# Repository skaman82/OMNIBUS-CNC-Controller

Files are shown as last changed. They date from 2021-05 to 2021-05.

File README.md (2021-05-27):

# OMNIBUS-CNC-Controller (WORK IN PROGRESS)
CNC Control Project (GRBL and ESTLCAM based). Please dont' sell the boards published here without my consent.

## OMNIBUS ESTLCAM Controller</br>
### FINISHED
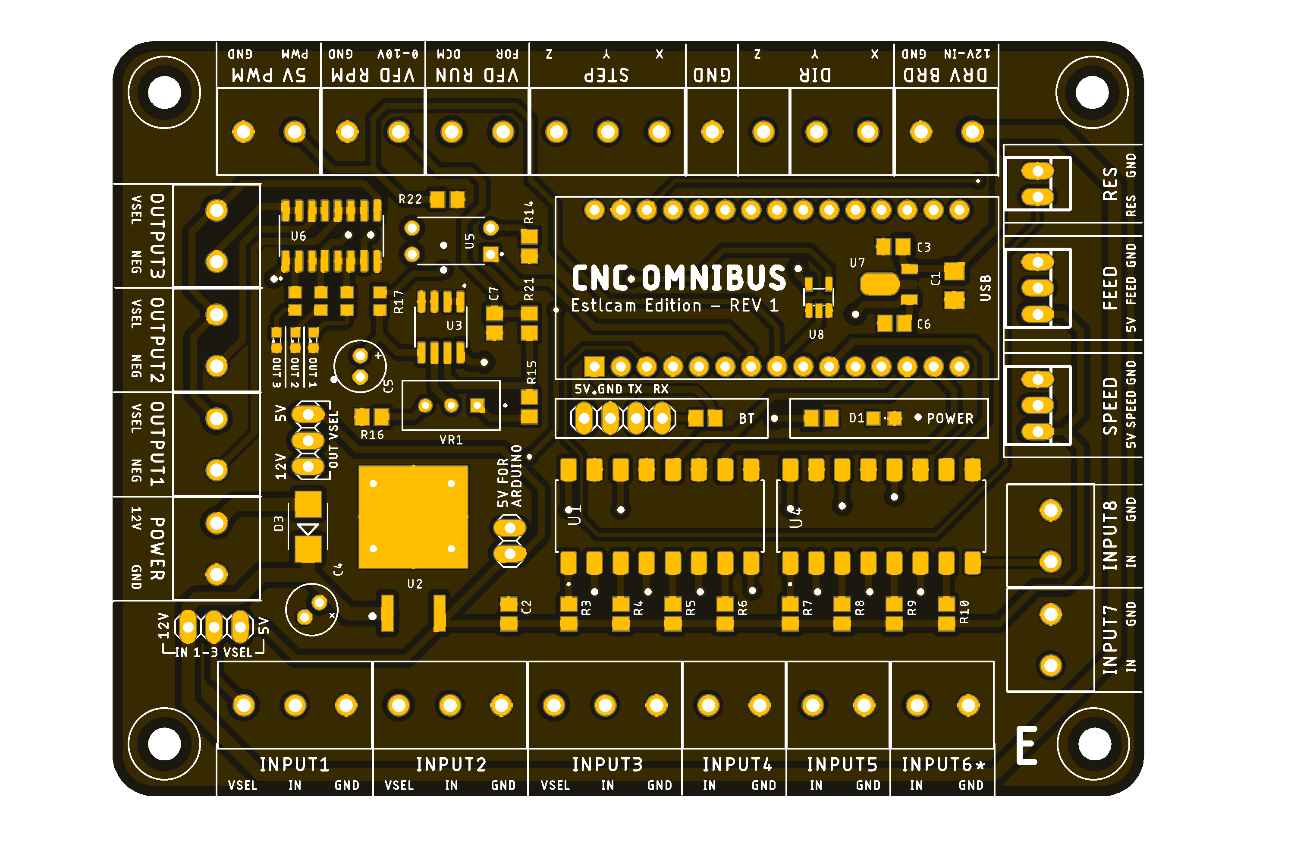
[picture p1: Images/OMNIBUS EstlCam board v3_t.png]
</br>
• 8 inputs for sensors and buttons (IN6 is usable if you remoove the LED "L" from the Nano)</br>
• All inputs are isolated with optocouplers</br>
• Inputs 1-3 have selectable voltage (5/12v) so you can connect inductive proximity sensors directly</br>
• VFD outputs (Spindle ON/OFF and RPM control)</br>
• 5V PWM output</br>
• 3 Outputs for relays - the outputs have selectable voltage (5/12v) - OUT3 is automatically enabled on spindle ON</br>
• Feed/Speed override connectors (JST XH 3P)</br>
• Header for bluetooth serial module (HC-05)</br>
• Screw-Terminals for easy connection</br>
• Connector for the DRV-Shield</br>
</br>
## OMNIBUS GRBL 1.1 Controller - also ESTLCAM compatible</br>
### FINISHED
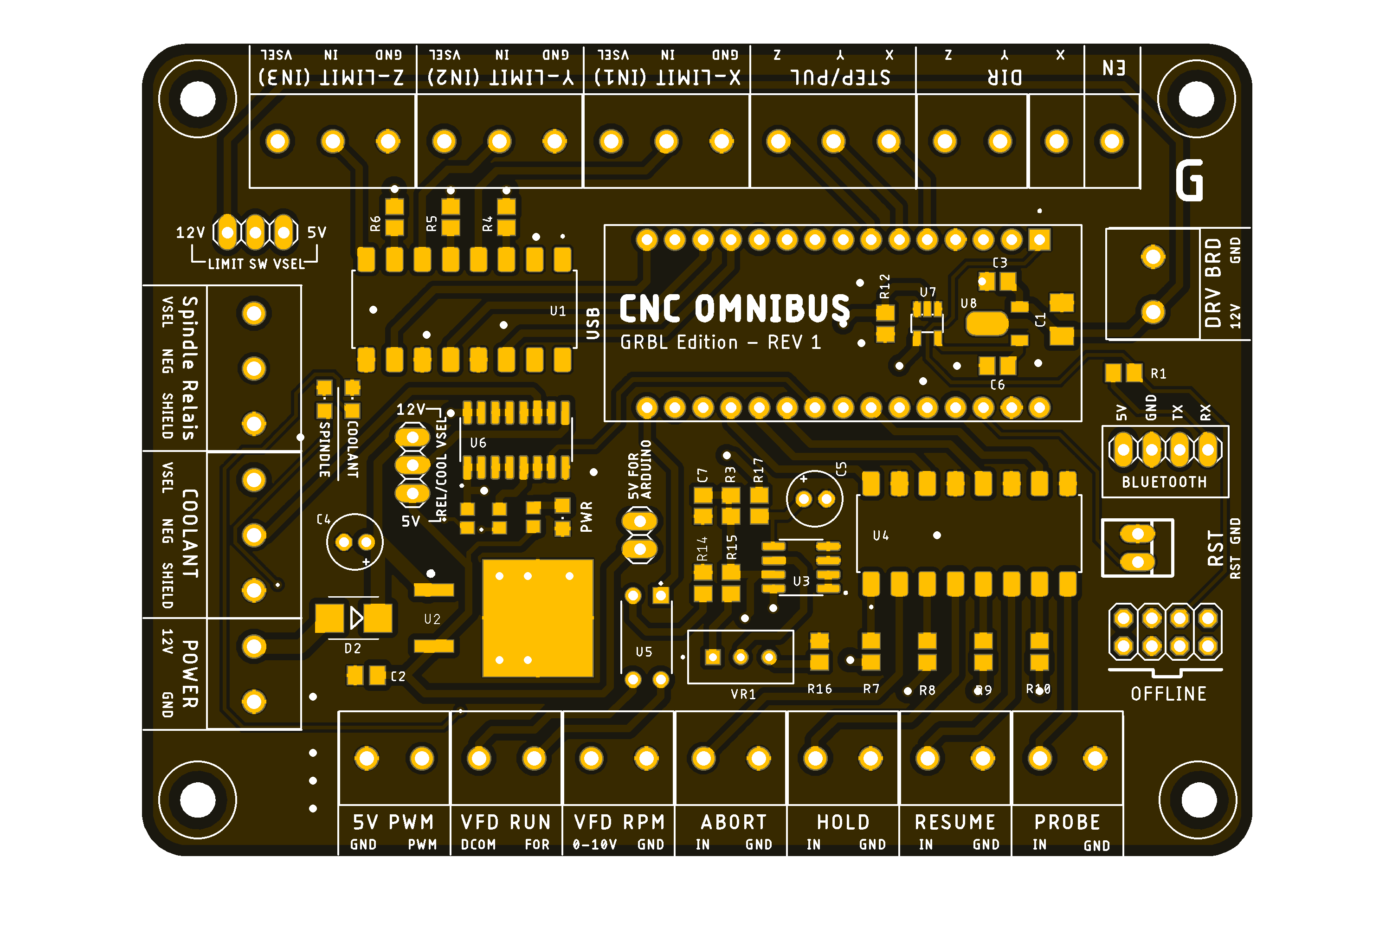
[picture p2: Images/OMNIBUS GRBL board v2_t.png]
</br>
• Limit-Inputs XYZ have selectable voltage (5/12v) so you can connect inductive proximity sensors directly</br>
• ABORT/HOLD/RESUME/PROBE inputs</br>
• All inputs are isolated with optocouplers</br>
• VFD outputs (Spindle ON/OFF and RPM control)</br>
• 5V PWM Output</br>
• 2 Outputs for relay (SPINDLE_RELAIS / COOLANT) - the outputs have selectable voltage (5/12v) - SPINDLE RELAY is automatically enabled on spindle ON</br>
• Header for bluetooth serial module (HC-05)</br>
• Header for offline controller</br>
• Screw-Terminals for easy connection</br>
• Connector for the DRV-Shield</br>

NOTE: To use the "SPINDLE RELAY" and "VFD RUN" Outputs, please uncomment "define USE_SPINDLE_DIR_AS_ENABLE_PIN" in the GRBL config.h file.
</br>
## OMNIBUS DRV SHIELD (mounts on top the controll PCB with spacers)</br>
### Experimental stage
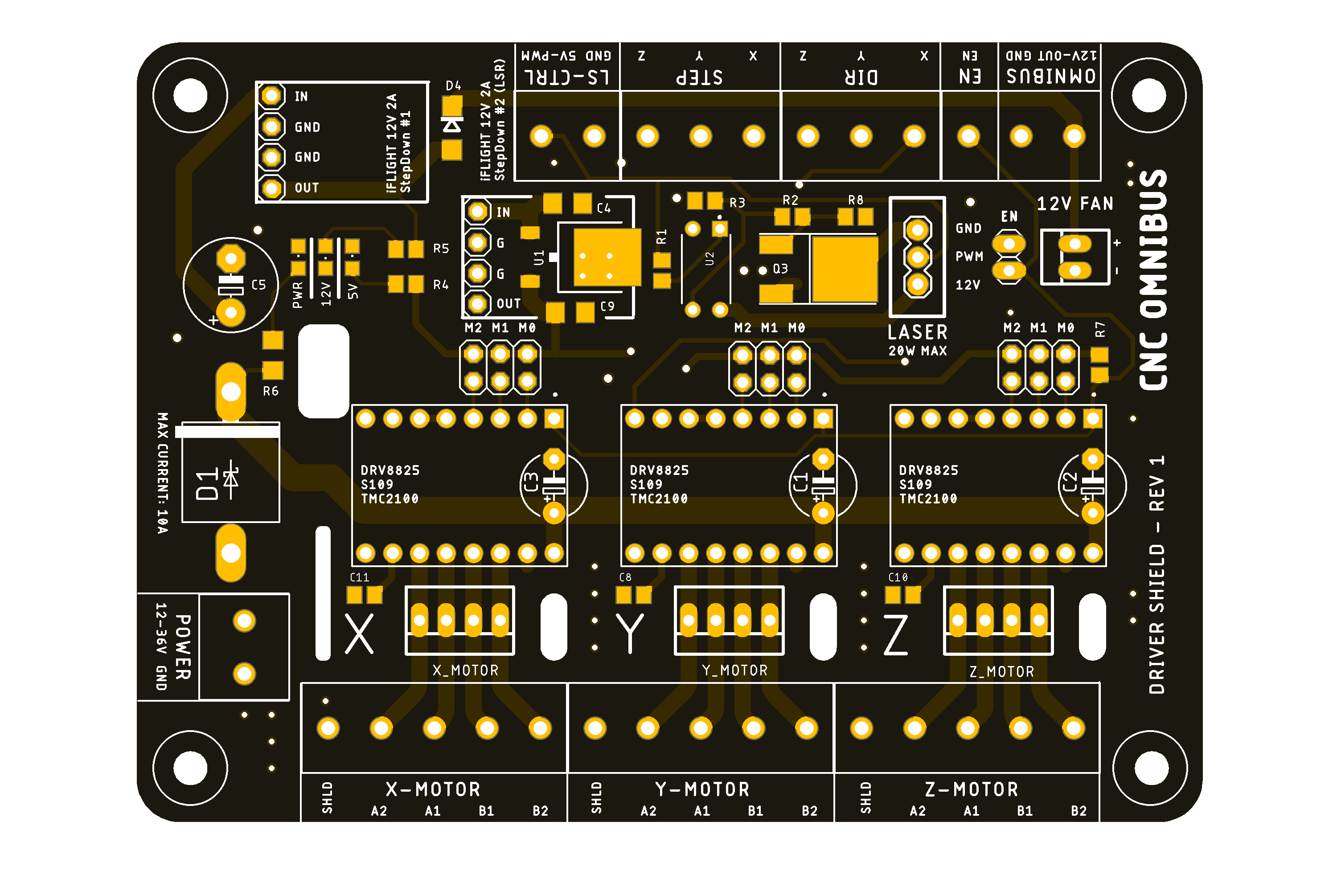
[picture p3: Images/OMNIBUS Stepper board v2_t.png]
</br>
• Up to 10A current support (2oz copper PCB required)</br>
• 3-Axis stepper driver support (DRV8825/S109/TMC2100) with stepping config jumpers</br>
• Header for laser module (3p)</br>
• Laser module safety switch - PWM controlled</br>
• Header for an extra 12V 2A BEC to power a laser module (20w max)</br>
• 12V fan header</br>
• 12V Power supply for the OMNIBUS controller (so you don't need an extra 12v PSU for the controll board)</br>
• Screw-Terminals for easy connection</br>

NOTE: If powerting the OMNIBUS Controller with the DRV Shield, use a heatsink on the 12V LDO and provide good airflow - the LDO is getting hot and will
shut down if thermal protection kicks in.

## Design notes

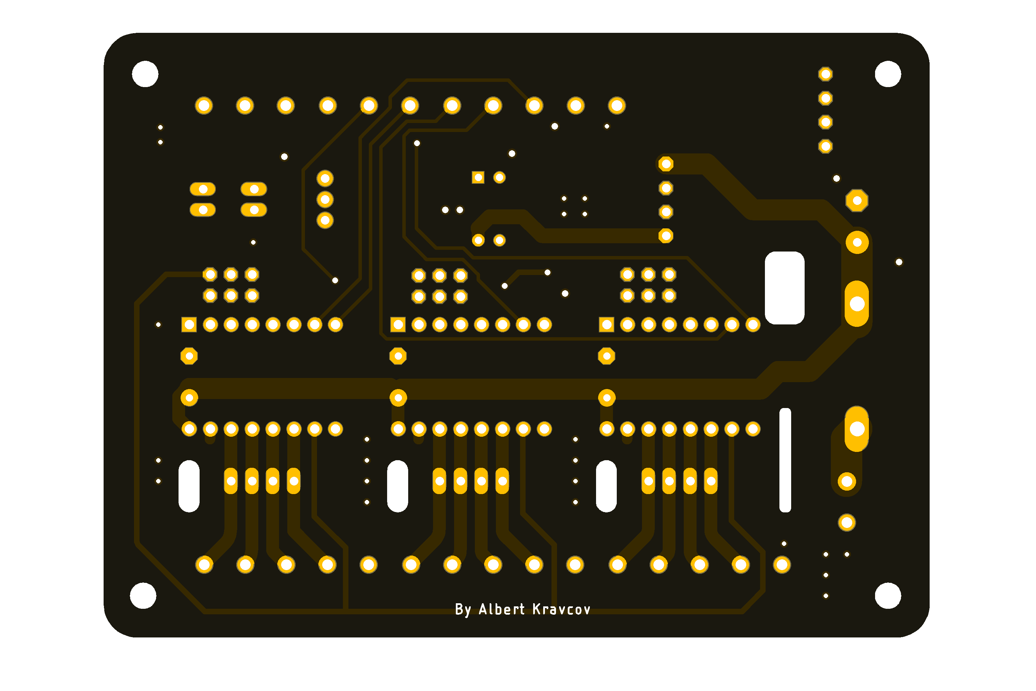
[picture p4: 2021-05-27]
Images/OMNIBUS Stepper board v2_b.png

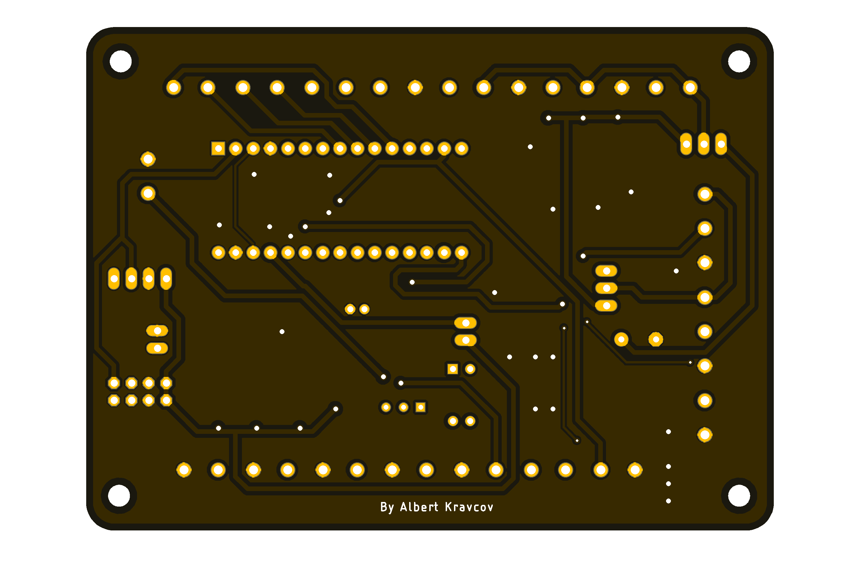
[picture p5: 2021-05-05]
Images/OMNIBUS GRBL board v2_b.png

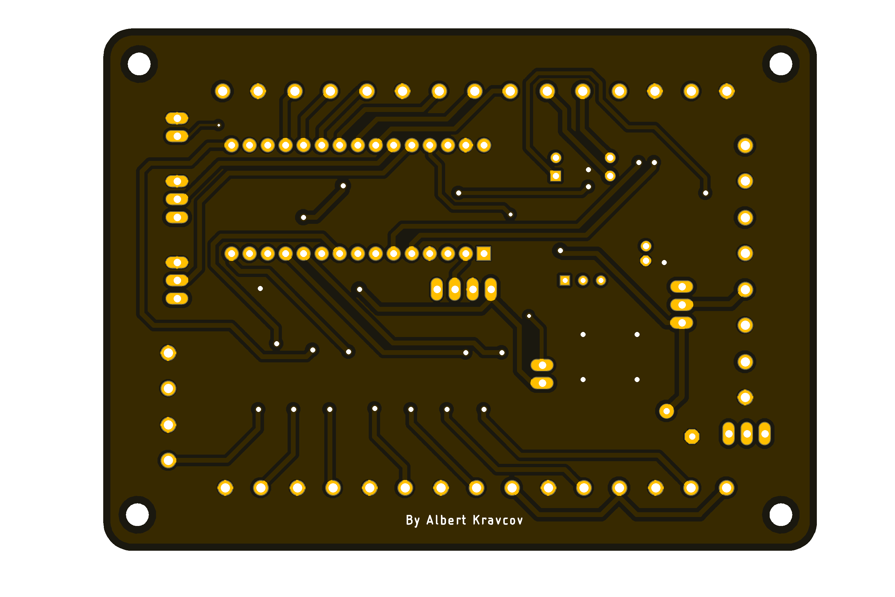
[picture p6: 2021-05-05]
Images/OMNIBUS EstlCam board v3_b.png

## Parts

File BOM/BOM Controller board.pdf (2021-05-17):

### EstlCam board v3

Part | Value | Device | Package | Description | price
BT | 2.54 pin header | PINHD-1X4 | 1X04 | PIN HEADER | 0
C1 | 0.33uF 50v | C-EUC1206 | C1206 Tantal | CAPACITOR, European symbol | 1,18
C2 | 100nf | C-EUC0805 | C0805 | CAPACITOR, European symbol | 0,054
C3 | 100nf | C-EUC0805 | C0805 | CAPACITOR, European symbol | 0,054
C4 | 220uf 25v | CPOL-EUE5-6 | E5-6 | POLARIZED CAPACITOR, European symbol | 0,52
C5 | 22uf | CPOL-EUE2-5 | E2-5 | POLARIZED CAPACITOR, European symbol | 0,52
C6 | 100nf | C-EUC0805 | C0805 | CAPACITOR, European symbol | 0,054
C7 | 100nf | C-EUC0805 | C0805 | CAPACITOR, European symbol | 0,054
D1 | green | LED1206 | LED-1206 | LED (Generic) | 0,23
D3 | SS36 | ES2D | SMB | DIODE | 0,34
IN1 | KF301-2P | 691131710002 | 691131710002 | WR-TBL Terminal block - CUU5/2 CUU5/2GR - 2 Pins;=>Code : Con_TBL_Screw_PClamp_5.00_6911317100xx_691131710002 | 0,125
IN2 | KF301-2P | 691131710002 | 691131710002 | WR-TBL Terminal block - CUU5/2 CUU5/2GR - 2 Pins;=>Code : Con_TBL_Screw_PClamp_5.00_6911317100xx_691131710002 | 0,125
IN3 | KF301-2P | 691131710002 | 691131710002 | WR-TBL Terminal block - CUU5/2 CUU5/2GR - 2 Pins;=>Code : Con_TBL_Screw_PClamp_5.00_6911317100xx_691131710002 | 0,125
IN4 | KF301-2P | 691131710002 | 691131710002 | WR-TBL Terminal block - CUU5/2 CUU5/2GR - 2 Pins;=>Code : Con_TBL_Screw_PClamp_5.00_6911317100xx_691131710002 | 0,125
IN5 | KF301-2P | 691131710002 | 691131710002 | WR-TBL Terminal block - CUU5/2 CUU5/2GR - 2 Pins;=>Code : Con_TBL_Screw_PClamp_5.00_6911317100xx_691131710002 | 0,125
IN6 | KF301-2P | 691131710002 | 691131710002 | WR-TBL Terminal block - CUU5/2 CUU5/2GR - 2 Pins;=>Code : Con_TBL_Screw_PClamp_5.00_6911317100xx_691131710002 | 0,125
IN_V_SEL | 2.54 pin header | PINHD-1X3 | 1X03 | PIN HEADER | 0
JP1 | 2.54 pin header | PINHD-1X2 | 1X02 | PIN HEADER | 0
IN7 | KF301-2P | 691131710002 | 691131710002 | WR-TBL Terminal block - CUU5/2 CUU5/2GR - 2 Pins;=>Code : Con_TBL_Screw_PClamp_5.00_6911317100xx_691131710002 | 0,125
IN8 | KF301-3P | 691131710003 | 691131710003 | WR-TBL Terminal block - CUU5/3 - 3 Pins;=>Code : | 0,125
DIR1 | KF301-3P | 691131710003 | 691131710003 | WR-TBL Terminal block - CUU5/3 - 3 Pins;=>Code : | 0,125
DIR2 | KF301-3P | 691131710003 | 691131710003 | WR-TBL Terminal block - CUU5/3 - 3 Pins;=>Code : | 0,125
LED2 | red | LED_ESML0603 | LED_SML0603 | LED | 0,23
LED3 | red | LED_ESML0603 | LED_SML0603 | LED | 0,23
LED4 | red | LED_ESML0603 | LED_SML0603 | LED | 0,23
OUT3 | KF301-2P | 691131710002 | 691131710002 | WR-TBL Terminal block - CUU5/2 CUU5/2GR - 2 Pins;=>Code : Con_TBL_Screw_PClamp_5.00_6911317100xx_691131710002 | 0,125
VFD | KF301-2P | 691131710002 | 691131710002 | WR-TBL Terminal block - CUU5/2 CUU5/2GR - 2 Pins;=>Code : Con_TBL_Screw_PClamp_5.00_6911317100xx_691131710002 | 0,125
RPM | KF301-2P | 691131710002 | 691131710002 | WR-TBL Terminal block - CUU5/2 CUU5/2GR - 2 Pins;=>Code : Con_TBL_Screw_PClamp_5.00_6911317100xx_691131710002 | 0,125
PWM | KF301-2P | 691131710002 | 691131710002 | WR-TBL Terminal block - CUU5/2 CUU5/2GR - 2 Pins;=>Code : Con_TBL_Screw_PClamp_5.00_6911317100xx_691131710002 | 0,125
OUT1 | KF301-2P | 691131710002 | 691131710002 | WR-TBL Terminal block - CUU5/2 CUU5/2GR - 2 Pins;=>Code : Con_TBL_Screw_PClamp_5.00_6911317100xx_691131710002 | 0,125
POW | KF301-2P | 691131710002 | 691131710002 | WR-TBL Terminal block - CUU5/2 CUU5/2GR - 2 Pins;=>Code : Con_TBL_Screw_PClamp_5.00_6911317100xx_691131710002 | 0,125
OUT_V_SEL | 2.54 pin header | PINHD-1X3 | 1X03 | PIN HEADER | 0
PWM | KF301-2P | 691131710002 | 691131710002 | WR-TBL Terminal block - CUU5/2 CUU5/2GR - 2 Pins;=>Code : Con_TBL_Screw_PClamp_5.00_6911317100xx_691131710002 | 0,125
OUT2 | KF301-2P | 691131710002 | 691131710002 | WR-TBL Terminal block - CUU5/2 CUU5/2GR - 2 Pins;=>Code : Con_TBL_Screw_PClamp_5.00_6911317100xx_691131710002 | 0,125
R1 | 1k | R-EU_R0805 | R0805 | RESISTOR, European symbol | 0,036
R2 | 220 | R-EU_R0805 | R0805 | RESISTOR, European symbol | 0,036
R3 | 220 | R-EU_R0805 | R0805 | RESISTOR, European symbol | 0,036
R4 | 220 | R-EU_R0805 | R0805 | RESISTOR, European symbol | 0,036
R5 | 220 | R-EU_R0805 | R0805 | RESISTOR, European symbol | 0,036
R6 | 220 | R-EU_R0805 | R0805 | RESISTOR, European symbol | 0,036
R7 | 220 | R-EU_R0805 | R0805 | RESISTOR, European symbol | 0,036
R8 | 220 | R-EU_R0805 | R0805 | RESISTOR, European symbol | 0,036
R9 | 220 | R-EU_R0805 | R0805 | RESISTOR, European symbol | 0,036
R10 | 220 | R-EU_R0805 | R0805 | RESISTOR, European symbol | 0,036
R11 | 220 | R-EU_R0603 | R0603 | RESISTOR, European symbol | 0,036
R12 | 220 | R-EU_R0603 | R0603 | RESISTOR, European symbol | 0,036
R13 | 220 | R-EU_R0603 | R0603 | RESISTOR, European symbol | 0,036
R14 | 220 | R-EU_R0805 | R0805 | RESISTOR, European symbol | 0,036
R15 | 1k | R-EU_R0805 | R0805 | RESISTOR, European symbol | 0,036
R16 | 1k | R-EU_R0805 | R0805 | RESISTOR, European symbol | 0,036
R17 | 4k7 | R-EU_R0603 | R0603 | RESISTOR, European symbol | 0,036
R21 | 1k | R-EU_R0805 | R0805 | RESISTOR, European symbol | 0,036
R22 | 4k7 | R-EU_R0805 | R0805 | RESISTOR, European symbol | 0,036
FEED | jst xh 3p | 22-23-2031 | 22-23-2031 | .100 (2.54mm) Center Header - 3 Pin" | 0,255
RESET | jst xh 2p | 22-23-2021 | 22-23-2021 | .100 (2.54mm) Center Header - 2 Pin" | 0,255
SPEED | jst xh 3p | 22-23-2031 | 22-23-2031 | .100 (2.54mm) Center Header - 3 Pin" | 0,255
STEP | KF301-3P | 691131710003 | 691131710003 | WR-TBL Terminal block - CUU5/3 - 3 Pins;=>Code : | 0,125
TB1 | Pin-Header FEM | ARDUINO_NANO | SHIELD_ARDUINO_NANO | Arduino Nano, Through Hole | 1,0
U1 | LTV-847S | LTV-847S | SOIC254P1016X460-16N | Optocoupler DC-IN 4-CH Transistor DC-OUT 16-Pin PDIP SMD Check prices | 1,08
U2 | MC7805C | MC7805C | TO254P1515X470-3N | 5V Positive voltage regulator ICs Check prices | 2,29
U3 | LM358M/NOPB | LM358M/NOPB | SOIC127P599X175-8N | Check prices Check prices | 0,25
U4 | LTV-847S | LTV-847S | SOIC254P1016X460-16N | Optocoupler DC-IN 4-CH Transistor DC-OUT 16-Pin PDIP SMD Check prices | 1,08
U5 | PC817X3NSZ1B | PC817X3NSZ1B | DIP762W50P254L495H455Q4 | Optoisolator Transistor Output 1 Channel 4-DIP Check prices | 0,299
U6 | ULN2003AD | ULN2003AD | SOIC127P600X175-16N | Check prices | 0,27
U7 | L78L05ACU | L78L05ACU | SOT89 | 5V Positive voltage regulator SMD SOT89 Package 100mA | 0,6
U8 | 74AHC1G125 | SN74AHC1G125DCKR SOT23-5L | | | 0,375
VR1 | 10k | W103 | TRIM_POT | Res Cermet Trimmer10K Ohm 10% 0.5W 25(Elec)Turn 2.19mm (9.53 X 4.83 X 11.55mm) Pin Thru-Hole Tube Check prices | 1,9
JP | 3x | | 2.54 Headers and Jumpers | | 0,204
HT | Heatsink | 10x10x10mm | Heatsink | | 0,41
PCB | pcb fab | pcb+stencil cost | | | 3
POS | Montage und Tests | | | | 10
| | | | | BOM € | 30,278

1

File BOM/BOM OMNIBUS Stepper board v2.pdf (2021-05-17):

### OMNIBUS Stepper board v2

Part | Value | Device | Package | Description | Price
5V | green | LEDCHIPLED_0805 | CHIPLED_0805 | LED | 0,23
12V | green | LEDCHIPLED_0805 | CHIPLED_0805 | LED | 0,23
C1 | 100uf 50V | CPOL-EUE5-6 | E5-6 | POLARIZED CAPACITOR, European symbol | 1
C2 | 100uf 50V | CPOL-EUE5-6 | E5-6 | POLARIZED CAPACITOR, European symbol | 1
C3 | 100uf 50V | CPOL-EUE5-6 | E5-6 | POLARIZED CAPACITOR, European symbol | 1
C4 | 0.33uf | C-EUC1206 Tantal | C1206 | CAPACITOR, European symbol | 1,18
C5 | 100uf 50v | CPOL-EUE5-8.5 | E5-8,5 | POLARIZED CAPACITOR, European symbol | 0,5
C6 | 0.33uf 50v | C-EUC1206 Tantal | C1206 | CAPACITOR, European symbol | 1,18
C7 | 100nf | C-EUC0805 | C0805 | CAPACITOR, European symbol | 0,054
C8 | 100nf | C-EUC0805 | C0805 | CAPACITOR, European symbol | 0,054
C9 | 100nf | C-EUC1206 | C1206 | CAPACITOR, European symbol | 0,054
C10 | 100nf | C-EUC0805 | C0805 | CAPACITOR, European symbol | 0,054
C11 | 100nf | C-EUC0805 | C0805 | CAPACITOR, European symbol | 0,054
D1 | 10SQ045 | 10SQ050 | DIOAD885W125L910D885 | | 1
D2 | SS310 | SS310 | DO-214AC | SCHOTTKY DIODES 40Vpeak, 28Vrms 5A (SBD) SMA(DO-214AC) | 0,1
D4 | SS310 | SS310 | DO-214AC | SCHOTTKY DIODES 40Vpeak, 28Vrms 5A (SBD) SMA(DO-214AC) | 0,1
DIR | KF301-3P | 691131710003 | 691131710003 | WR-TBL Terminal block - CUU5/3 - 3 Pins;=>Code : | 0,125
EN-LOW | pin header and jumper | PINHD-1X2 | 1X02 | PIN HEADER | 0
FAN | JST XH 2p | 22-23-2021 | 22-23-2021 | .100 (2.54mm) Center Header - 2 Pin" | 0,255
J1 | JST XH 3p | CONN_03 | 1X03 | Multi connection point. Often used as Generic Header-pin footprint for 0.1 inch spaced/style header connections | 0,255
JP1 | BEC wire | PINHD-1X1 | 1X01 | PIN HEADER | 0
JP2 | BEC wire | PINHD-1X1 | 1X01 | PIN HEADER | 0
JP3 | BEC wire | PINHD-1X1 | 1X01 | PIN HEADER | 0
JP4 | BEC wire | PINHD-1X1 | 1X01 | PIN HEADER | 0
JP_X | pin header double row | PINHD-2X3 | 2X03 | PIN HEADER | 0,2
JP_Y | pin header double row | PINHD-2X3 | 2X03 | PIN HEADER | 0,2
JP_Z | pin header double row | PINHD-2X3 | 2X03 | PIN HEADER | 0,2
K7 | KF301-5P (or 2+3p) | 691131710005 | 691131710005 | WR-TBL Terminal block - CUU5/5 - 5 Pins;=>Code : Con_TBL_Screw_PClamp_5.00_6911317100xx_691131710005 | 0,25
K8 | KF301-5P (or 2+3p) | 691131710005 | 691131710005 | WR-TBL Terminal block - CUU5/5 - 5 Pins;=>Code : Con_TBL_Screw_PClamp_5.00_6911317100xx_691131710005 | 0,25
K9 | KF301-5P (or 2+3p) | 691131710005 | 691131710005 | WR-TBL Terminal block - CUU5/5 - 5 Pins;=>Code : Con_TBL_Screw_PClamp_5.00_6911317100xx_691131710005 | 0,25
LASER-ON | blue | LEDCHIPLED_0805 | CHIPLED_0805 | LED | 0,23
MIC2954 | MIC2954 | MIC2954 | SOT223 | 5V 250mA regulator | 1,024
POW | KF301-3P | 691131710003 | 691131710003 | WR-TBL Terminal block - CUU5/3 - 3 Pins;=>Code : | 0,125
PWR | green | LEDCHIPLED_0805 | CHIPLED_0805 | LED | 0,23
Q1 | BTS134D | FQD7N10LTM | TO-252 | MOSFET N-CH 100V 5.8A 350mOhm 6nC DPAK Check prices | 0,475
R1 | 1k | R-EU_R0805 | R0805 | RESISTOR, European symbol | 0,036
R2 | 10k | R-EU_R0805 | R0805 | RESISTOR, European symbol | 0,036
R3 | 470 | R-EU_R0805 | R0805 | RESISTOR, European symbol | 0,036
R4 | 330 | R-EU_R0805 | R0805 | RESISTOR, European symbol | 0,036
R5 | 1k | R-EU_R0805 | R0805 | RESISTOR, European symbol | 0,036
R6 | 1k | R-EU_R1206 | R1206 | RESISTOR, European symbol | 0,036
R7 | 1k | R-EU_R0805 | R0805 | RESISTOR, European symbol | 0,036
RAW | KF301-2P | 691131710002 | 691131710002 | WR-TBL Terminal block - CUU5/2 CUU5/2GR - 2 Pins;=>Code : Con_TBL_Screw_PClamp_5.00_6911317100xx_691131710002 | 0,125
PWM | KF301-2P | 691131710002 | 691131710002 | WR-TBL Terminal block - CUU5/2 CUU5/2GR - 2 Pins;=>Code : Con_TBL_Screw_PClamp_5.00_6911317100xx_691131710002 | 0,125
STEP | KF301-3P | 691131710003 | 691131710003 | WR-TBL Terminal block - CUU5/3 - 3 Pins;=>Code : | 0,125
U2 | L7805ACD2T-TR | L7805ACD2T-TR | TO254P1515X470-3N | 12V Positive voltage regulator ICs Check prices | 0,603
X | 2.54 FEM CON 2x | DRV8825_STEPPER_MOTOR_DRIVER_CARRIER | IC_DRV8825_STEPPER_MOTOR_DRIVER_CARRIER | Stepper motor controler; IC: DRV8825; 1.5A; Uin mot: 8.2÷45V | 0,5
X_MOTOR | JST XH 4p | 22-23-2041 | 22-23-2041 | .100 (2.54mm) Center Header - 4 Pin" | 0,255
Y | 2.54 FEM CON 2x | DRV8825_STEPPER_MOTOR_DRIVER_CARRIER | IC_DRV8825_STEPPER_MOTOR_DRIVER_CARRIER | Stepper motor controler; IC: DRV8825; 1.5A; Uin mot: 8.2÷45V | 0,5
Y_MOTOR | JST XH 4p | 22-23-2041 | 22-23-2041 | .100 (2.54mm) Center Header - 4 Pin" | 0,255
Z | 2.54 FEM CON 2x | DRV8825_STEPPER_MOTOR_DRIVER_CARRIER | IC_DRV8825_STEPPER_MOTOR_DRIVER_CARRIER | Stepper motor controler; IC: DRV8825; 1.5A; Uin mot: 8.2÷45V | 0,5
Z_MOTOR | JST XH 4p | 22-23-2041 | 22-23-2041 | .100 (2.54mm) Center Header - 4 Pin" | 0,255
PCB | FAB | | | | 3
MNT | Work | | | | 7
| | | | | BOM | 25,354

1

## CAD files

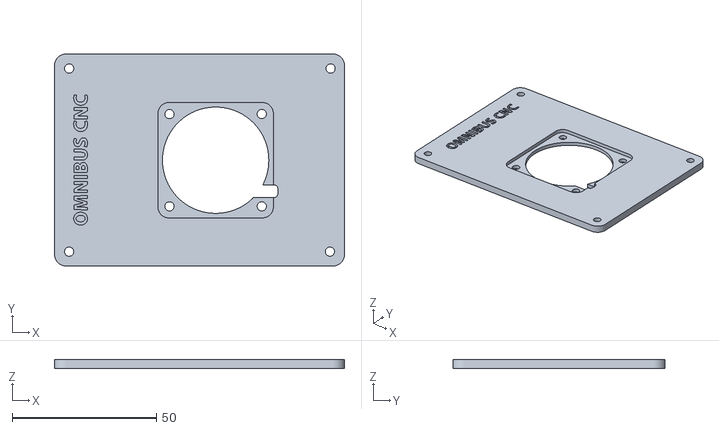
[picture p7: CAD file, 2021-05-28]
Fan holder 40mm/Fan holder_fixed.stl
100.6 x 73.6 x 3.00

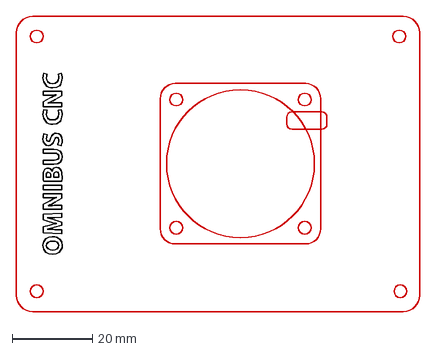
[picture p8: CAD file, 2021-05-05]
Fan holder 40mm/40mm fan holder.dxf
100.6 x 73.6 mm

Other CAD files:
Fan holder 40mm/Fan holder.stl

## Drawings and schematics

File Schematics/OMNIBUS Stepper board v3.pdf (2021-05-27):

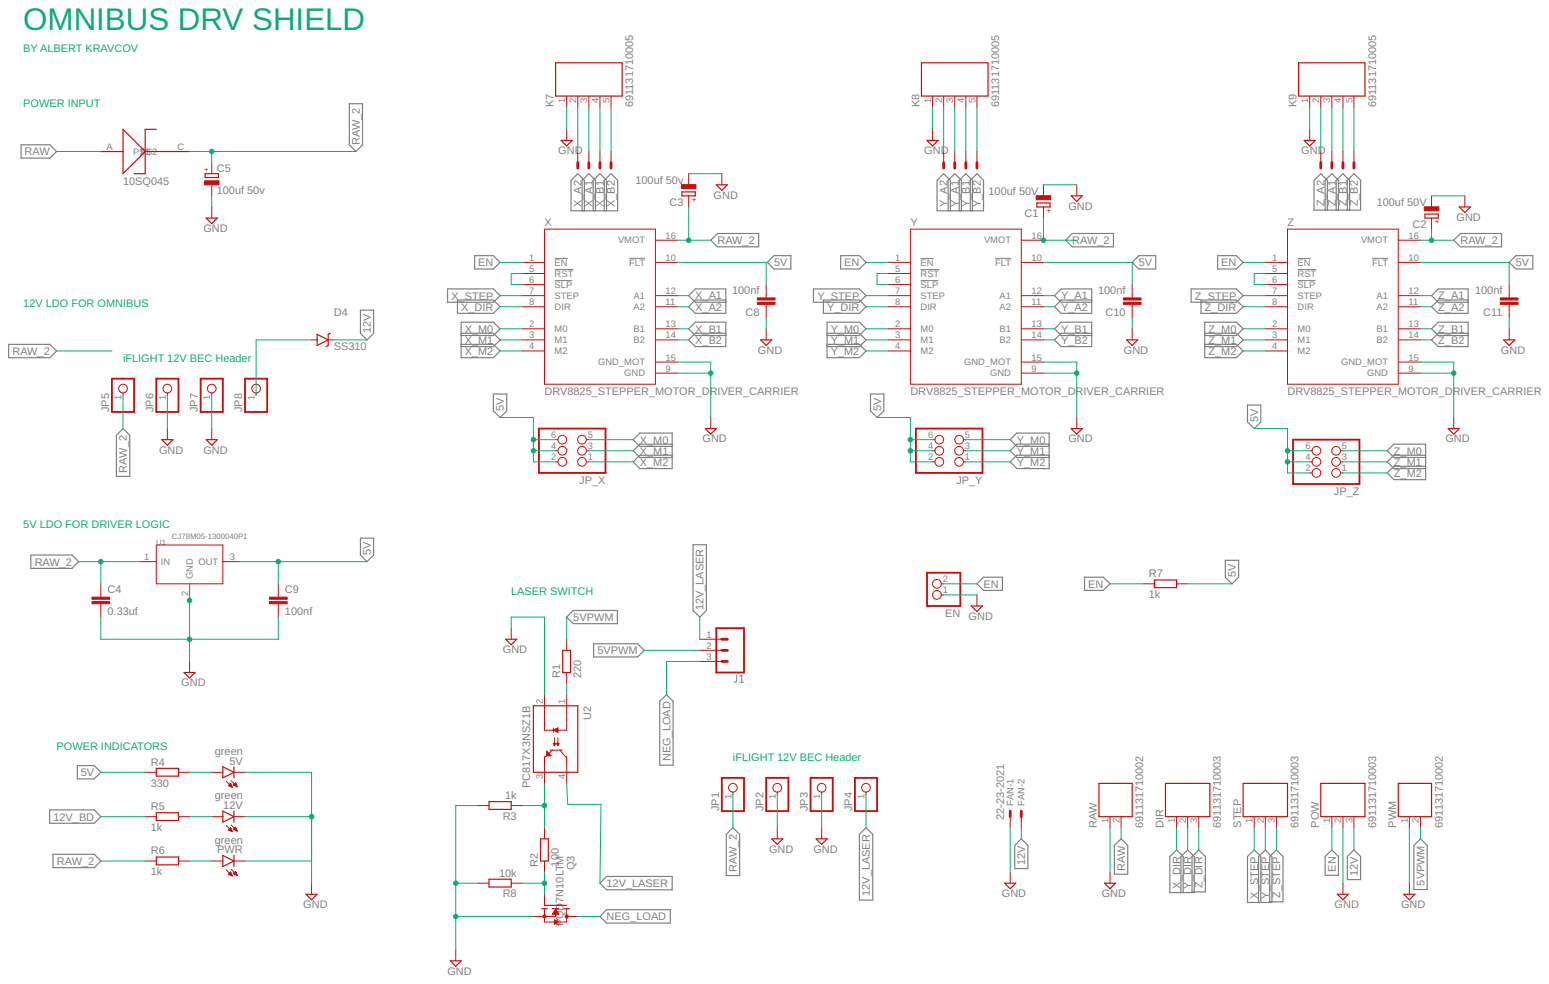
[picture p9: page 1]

5V LDO FOR DRIVER LOGIC

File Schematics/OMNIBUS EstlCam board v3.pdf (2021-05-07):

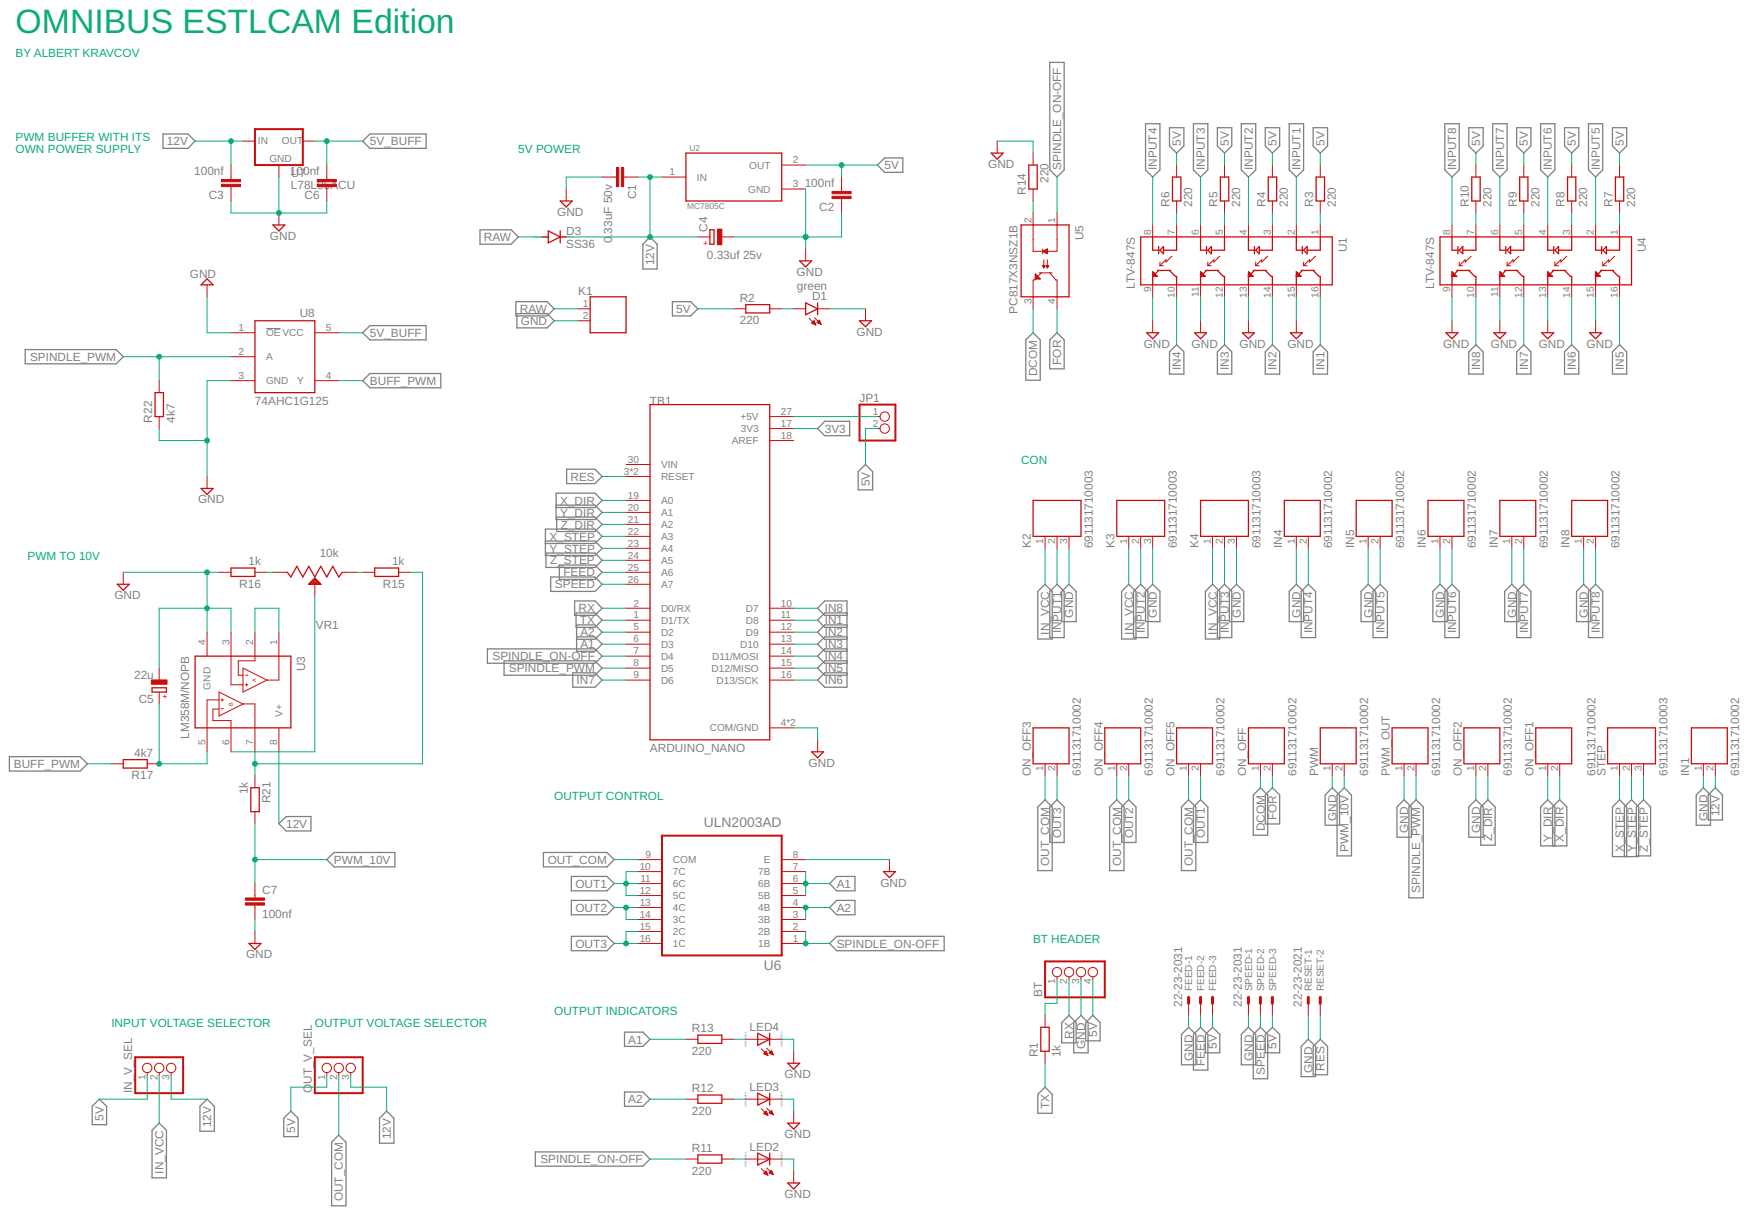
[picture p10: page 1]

PWM BUFFER WITH ITS OWN POWER SUPPLY

GND GND

GND GND GND GND GND

A1 SPINDLE_ON-OFF | 13 D11/MOSI 14 D12/MISO IN3 IN4 15

SPINDLE_PWM | IN5 16

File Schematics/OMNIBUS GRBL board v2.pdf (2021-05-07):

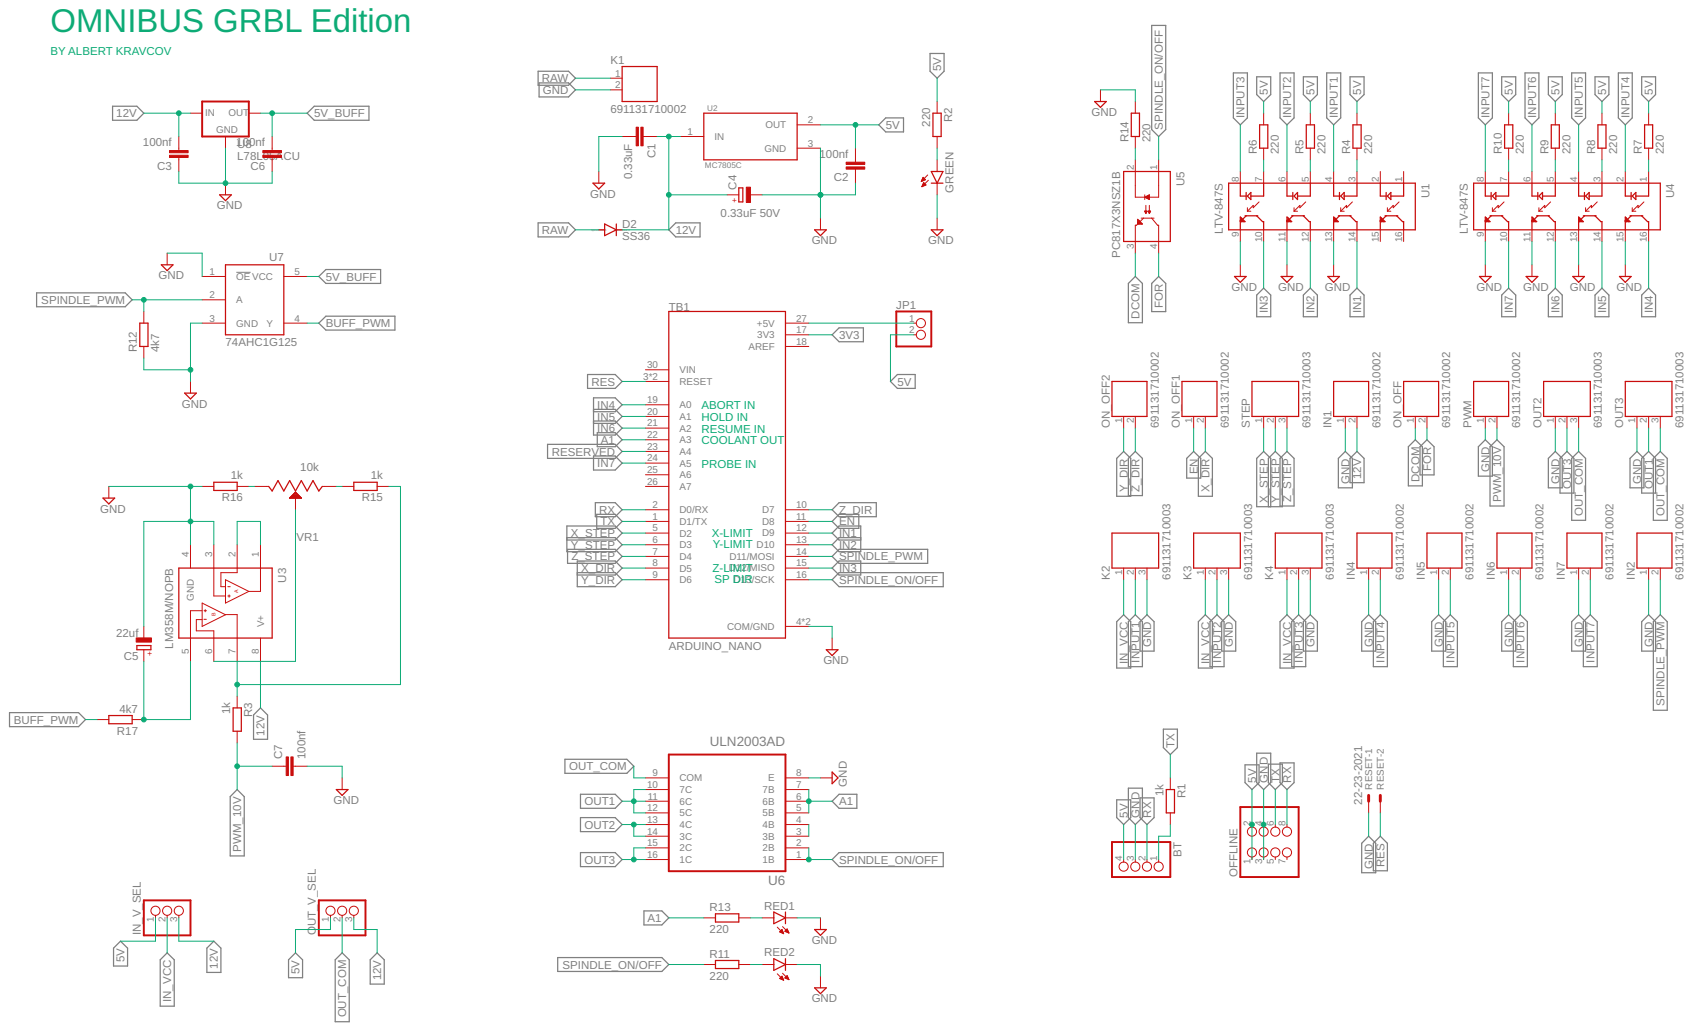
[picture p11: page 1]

ABORT IN
HOLD IN
RESUME IN
COOLANT OUT PROBE IN

11 | 6
12 | 5

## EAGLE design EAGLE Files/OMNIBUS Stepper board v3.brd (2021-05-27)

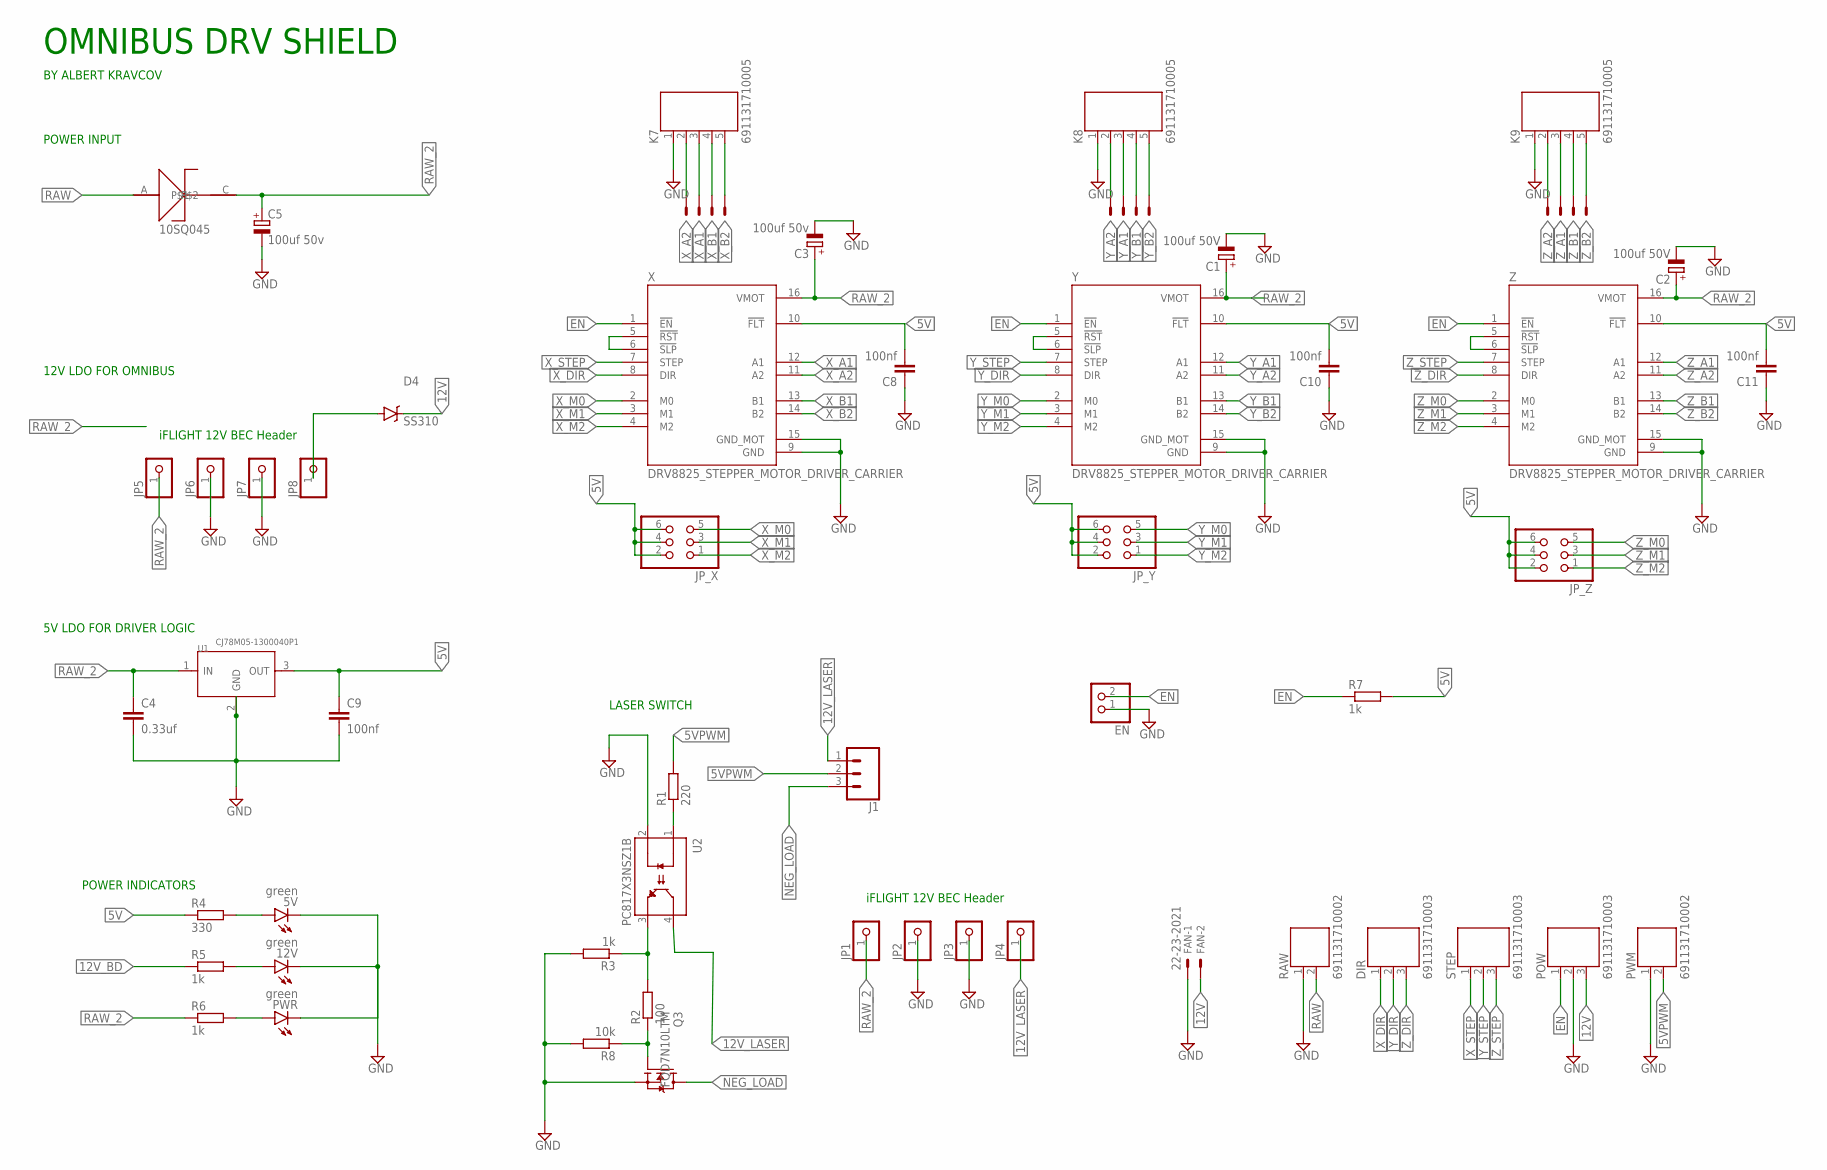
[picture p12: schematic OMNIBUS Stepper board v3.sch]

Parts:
5V, 12V: green; CHIPLED_0805
C1, C2: 100uf 50V; E5-6
C3: 100uf 50v; E5-6
C4: 0.33uf; C1206
C5: 100uf 50v; E5-8,5
C8, C10, C11: 100nf; C0805
C9: 100nf; C1206
D1: 10SQ045; DIOAD885W125L910D885
D4: SS310; DO-214AC
DIR: 691131710003
EN: PINHD-1X2; 1X02
FAN: 22-23-2021
J1: CONN_03; 1X03
JP1, JP2, JP3, JP4, JP5, JP6, JP7, JP8: PINHD-1X1; 1X01
JP_X: PINHD-2X3; 2X03
JP_Y: PINHD-2X3; 2X03
JP_Z: PINHD-2X3; 2X03
K7, K8, K9: 691131710005
POW: 691131710003
PWM: 691131710002
PWR: green; CHIPLED_0805
Q3: FQD7N10LTM; TO-252
R1: 220; R0805
R2: 100; R0805
R3, R5, R7: 1k; R0805
R4: 330; R0805
R6: 1k; R1206
R8: 10k; R0805
RAW: 691131710002
STEP: 691131710003
U1: CJ78M05-1300040P1; TO252
U2: PC817X3NSZ1B; DIP762W50P254L495H455Q4
X: DRV8825_STEPPER_MOTOR_DRIVER_CARRIER; IC_DRV8825_STEPPER_MOTOR_DRIVER_CARRIER
X_MOTOR: 22-23-2041
Y: DRV8825_STEPPER_MOTOR_DRIVER_CARRIER; IC_DRV8825_STEPPER_MOTOR_DRIVER_CARRIER
Y_MOTOR: 22-23-2041
Z: DRV8825_STEPPER_MOTOR_DRIVER_CARRIER; IC_DRV8825_STEPPER_MOTOR_DRIVER_CARRIER
Z_MOTOR: 22-23-2041

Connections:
5V: C8.2, C9.1, C10.2, C11.2, JP_X.2, JP_X.4, JP_X.6, JP_Y.2, JP_Y.4, JP_Y.6, JP_Z.2, JP_Z.4, JP_Z.6, R4.1, R7.2, U1.3 (OUT), X.10 (!FLT), Y.10 (!FLT), Z.10 (!FLT)
5VPWM: J1.2, PWM.2, R1.2
12V: D4.C, FAN.2, POW.3
12V_BD: D4.A, JP8.1, R5.1
12V_LASER: J1.1, JP4.1, U2.4 (COLLECTOR)
EN: EN.2, POW.1, R7.1, X.1 (!EN), Y.1 (!EN), Z.1 (!EN)
GND: 5V.C, 12V.C, C1.-, C2.-, C3.-, C4.2, C5.-, C8.1, C9.2, C10.1, C11.1, EN.1, FAN.1, JP2.1, JP3.1, JP6.1, JP7.1, K7.1, K8.1, K9.1, POW.2, PWM.1, PWR.C, Q3.3 (S), R3.2, R8.2, RAW.1, U1.2 (GND), U2.2 (CATHODE), X.9 (GND), X.15 (GND_MOT), Y.9 (GND), Y.15 (GND_MOT), Z.9 (GND), Z.15 (GND_MOT)
unnamed: Q3.1 (G), R2.1, R8.1
unnamed: 5V.A, R4.2
unnamed: R1.1, U2.1 (ANODE)
unnamed: R2.2, R3.1, U2.3 (EMITTER)
unnamed: 12V.A, R5.2
unnamed: PWR.A, R6.2
NC: Z.5 (!RST), Z.6 (!SLP)
NC2: Y.5 (!RST), Y.6 (!SLP)
NC3: X.5 (!RST), X.6 (!SLP)
NEG_LOAD: J1.3, Q3.T (D)
RAW: D1.A, RAW.2
RAW_2: C1.+, C2.+, C3.+, C4.1, C5.+, D1.C, JP1.1, JP5.1, R6.1, U1.1 (IN), X.16 (VMOT), Y.16 (VMOT), Z.16 (VMOT)
X_A1: K7.3, X.12 (A1), X_MOTOR.3
X_A2: K7.2, X.11 (A2), X_MOTOR.4
X_B1: K7.4, X.13 (B1), X_MOTOR.2
X_B2: K7.5, X.14 (B2), X_MOTOR.1
X_DIR: DIR.1, X.8 (DIR)
X_M0: JP_X.5, X.2 (M0)
X_M1: JP_X.3, X.3 (M1)
X_M2: JP_X.1, X.4 (M2)
X_STEP: STEP.1, X.7 (STEP)
Y_A1: K8.3, Y.12 (A1), Y_MOTOR.3
Y_A2: K8.2, Y.11 (A2), Y_MOTOR.4
Y_B1: K8.4, Y.13 (B1), Y_MOTOR.2
Y_B2: K8.5, Y.14 (B2), Y_MOTOR.1
Y_DIR: DIR.2, Y.8 (DIR)
Y_M0: JP_Y.5, Y.2 (M0)
Y_M1: JP_Y.3, Y.3 (M1)
Y_M2: JP_Y.1, Y.4 (M2)
Y_STEP: STEP.2, Y.7 (STEP)
Z_A1: K9.3, Z.12 (A1), Z_MOTOR.3
Z_A2: K9.2, Z.11 (A2), Z_MOTOR.4
Z_B1: K9.4, Z.13 (B1), Z_MOTOR.2
Z_B2: K9.5, Z.14 (B2), Z_MOTOR.1
Z_DIR: DIR.3, Z.8 (DIR)
Z_M0: JP_Z.5, Z.2 (M0)
Z_M1: JP_Z.3, Z.3 (M1)
Z_M2: JP_Z.1, Z.4 (M2)
Z_STEP: STEP.3, Z.7 (STEP)

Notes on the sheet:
LASER SWITCH
POWER INPUT
5V LDO FOR DRIVER LOGIC
12V LDO FOR OMNIBUS
POWER INDICATORS
iFLIGHT 12V BEC Header
OMNIBUS DRV SHIELD
BY ALBERT KRAVCOV
10SQ045

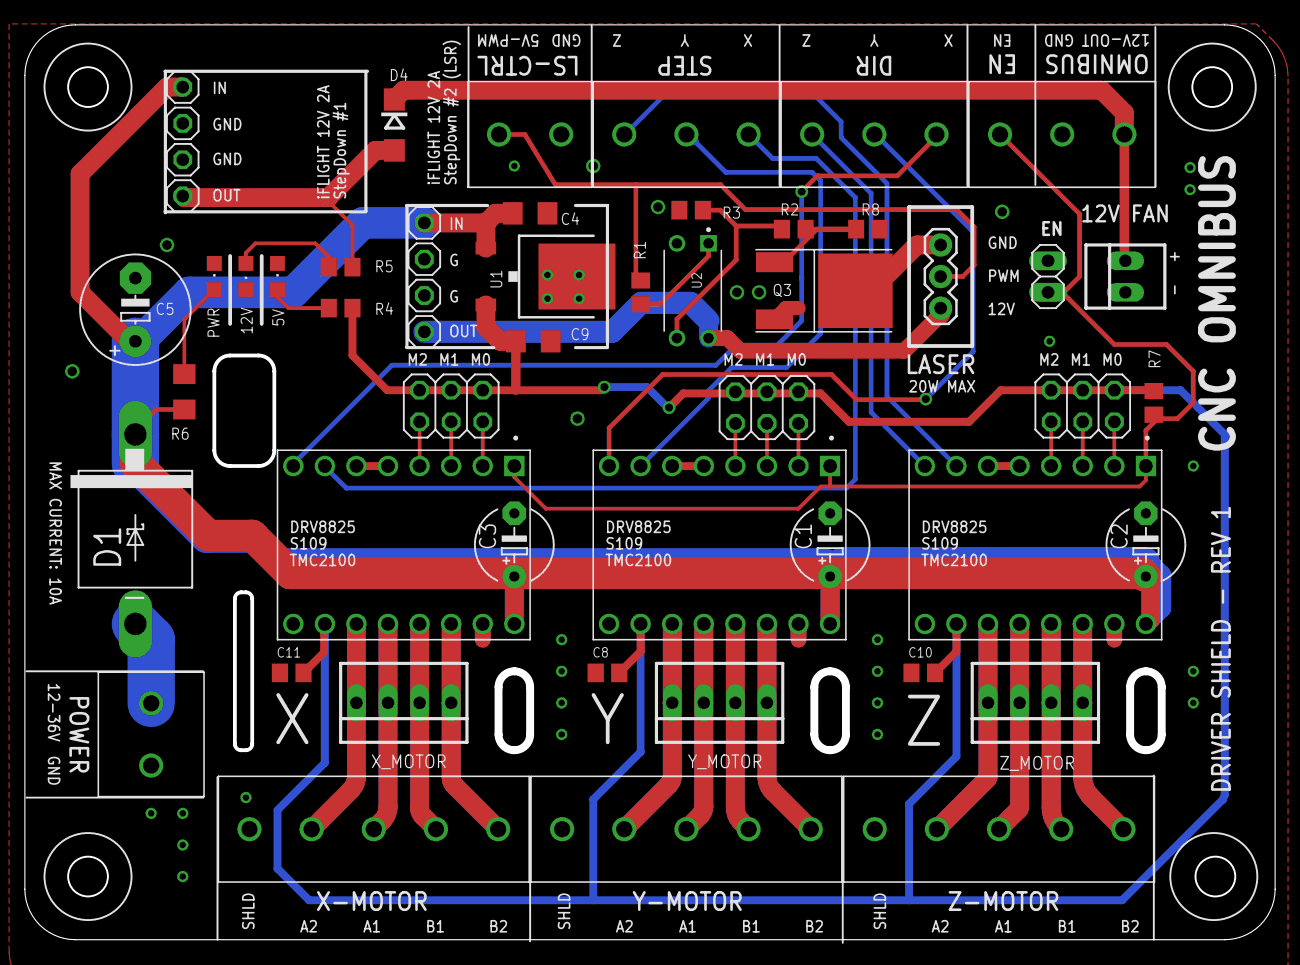
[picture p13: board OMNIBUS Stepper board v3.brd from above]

Board: 2 copper layers, 100.6 x 73.6 mm, 53 parts (0 on the bottom side), 46 nets.

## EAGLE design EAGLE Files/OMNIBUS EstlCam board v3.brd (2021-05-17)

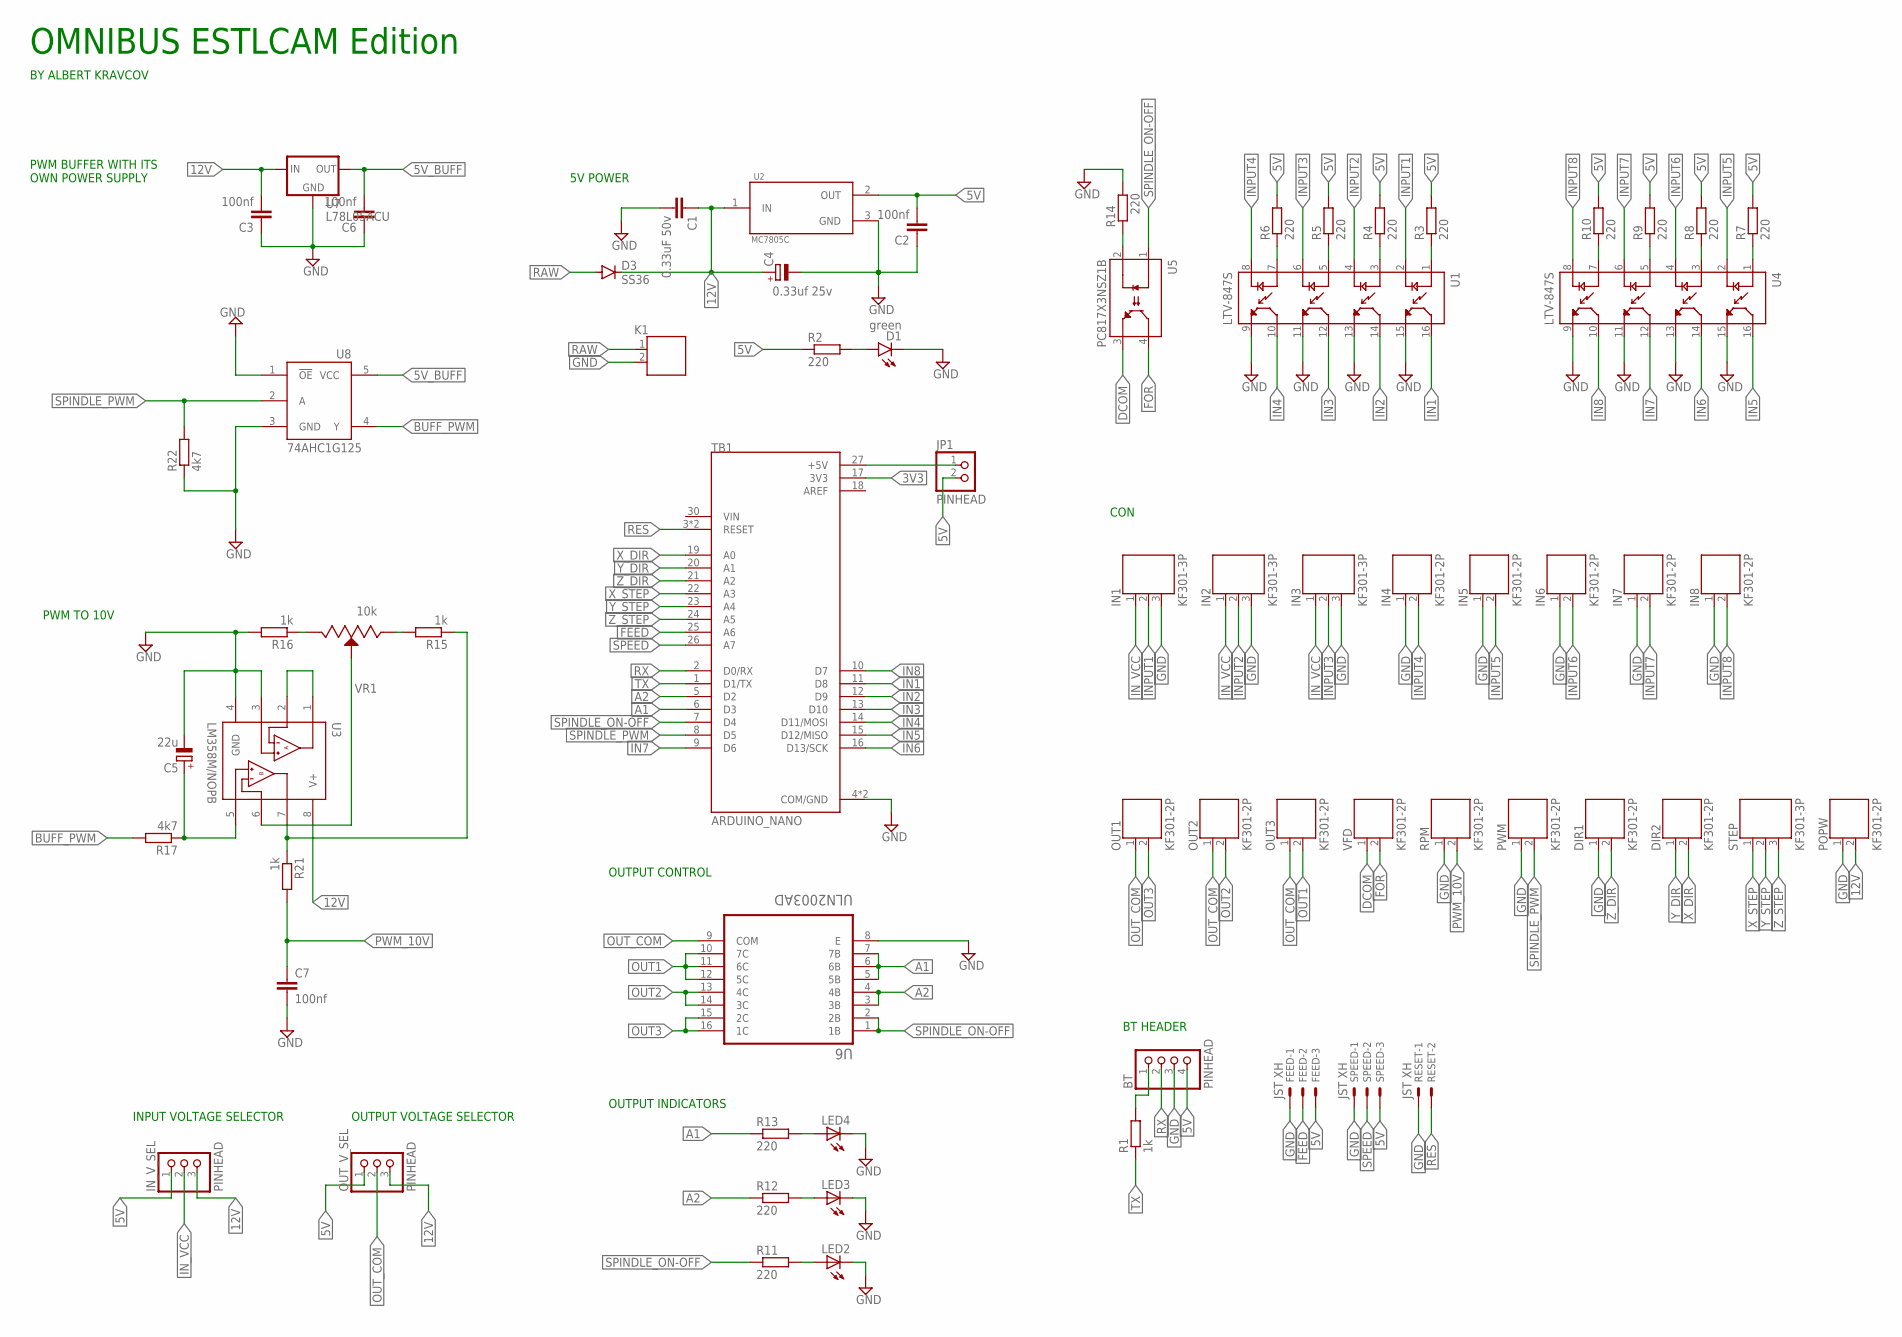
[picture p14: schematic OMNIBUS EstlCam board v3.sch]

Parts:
BT: PINHEAD; 1X04
C1: 0.33uF 50v; C1206
C2, C3, C6, C7: 100nf; C0805
C4: 0.33uf 25v; E2-5
C5: 22u; E2-5
D1: green; CHIPLED_0805
D3: SS36; SMB
DIR1, DIR2: KF301-2P; 691131710002
FEED: JST XH; 22-23-2031
IN1, IN2, IN3: KF301-3P; 691131710003
IN4, IN5, IN6, IN7, IN8: KF301-2P; 691131710002
IN_V_SEL: PINHEAD; 1X03
JP1: PINHEAD; 1X02
K1: 691131710002
LED2, LED3, LED4: LED_ESML0603; LED_SML0603
OUT1, OUT2, OUT3: KF301-2P; 691131710002
OUT_V_SEL: PINHEAD; 1X03
POPW: KF301-2P; 691131710002
PWM: KF301-2P; 691131710002
R1, R15, R16, R21: 1k; R0805
R2, R3, R4, R5, R6, R7, R8, R9, R10, R14: 220; R0805
R11, R12, R13: 220; R0603
R17: 4k7; R0603
R22: 4k7; R0805
RESET: JST XH; 22-23-2021
RPM: KF301-2P; 691131710002
SPEED: JST XH; 22-23-2031
STEP: KF301-3P; 691131710003
TB1: ARDUINO_NANO; SHIELD_ARDUINO_NANO
U1, U4: LTV-847S; SOIC254P1016X460-16N
U2: MC7805C; TO254P1515X470-3N
U3: LM358M/NOPB; SOIC127P599X175-8N
U5: PC817X3NSZ1B; DIP762W50P254L495H455Q4
U6: ULN2003AD; SOIC127P600X175-16N
U7: L78L05ACU; SOT89
U8: 74AHC1G125; SOT23-5L
VFD: KF301-2P; 691131710002
VR1: 10k; TRIM_3296W-1-502

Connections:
3V3: TB1.17 (3V3)
5V: BT.4, C2.2, FEED.3, IN_V_SEL.1, JP1.2, OUT_V_SEL.1, R2.1, R3.2, R4.2, R5.2, R6.2, R7.2, R8.2, R9.2, R10.2, SPEED.3, U2.2 (OUT)
5V_BUFF: C6.2, U7.1 (OUT), U8.5 (VCC)
12V: C1.1, C3.2, C4.+, D3.C, IN_V_SEL.3, OUT_V_SEL.3, POPW.2, U2.1 (IN), U3.8 (V+), U7.3 (IN)
A1: R13.1, TB1.6 (D3), U6.5 (5B), U6.6 (6B), U6.7 (7B)
A2: R12.1, TB1.5 (D2), U6.3 (3B), U6.4 (4B)
ARDU5V: JP1.1, TB1.27 (+5V)
AREF: TB1.18 (AREF)
BUFF_PWM: R17.2, U8.4 (Y)
D: R15.1, R21.1, U3.7 (OUTB)
DCOM: U5.3 (EMITTER), VFD.1
FEED: FEED.2, TB1.25 (A6)
FOR: U5.4 (COLLECTOR), VFD.2
GND: BT.3, C1.2, C2.1, C3.1, C4.-, C5.-, C6.1, C7.2, D1.C, DIR1.1, FEED.1, IN1.3, IN2.3, IN3.3, IN4.1, IN5.1, IN6.1, IN7.1, IN8.1, K1.2, LED2.C, LED3.C, LED4.C, POPW.1, PWM.1, R14.2, R16.2, R22.1, RESET.1, RPM.1, SPEED.1, TB1.4 (COM/GND), TB1.29 (COM/GND), U1.9 (ET3), U1.11 (ET2), U1.13 (ET1), U1.15 (ET), U2.3 (GND), U3.3 (+INA), U3.4 (GND), U4.9 (ET3), U4.11 (ET2), U4.13 (ET1), U4.15 (ET), U6.8 (E), U7.2 (GND), U8.1 (!OE), U8.3 (GND)
IN1: TB1.11 (D8), U1.16 (CT)
IN2: TB1.12 (D9), U1.14 (CT1)
IN3: TB1.13 (D10), U1.12 (CT2)
IN4: TB1.14 (D11/MOSI), U1.10 (CT3)
IN5: TB1.15 (D12/MISO), U4.16 (CT)
IN6: TB1.16 (D13/SCK), U4.14 (CT1)
IN7: TB1.9 (D6), U4.12 (CT2)
IN8: TB1.10 (D7), U4.10 (CT3)
INPUT1: IN1.2, U1.2 (C)
INPUT2: IN2.2, U1.4 (C1)
INPUT3: IN3.2, U1.6 (C2)
INPUT4: IN4.2, U1.8 (C3)
INPUT5: IN5.2, U4.2 (C)
INPUT6: IN6.2, U4.4 (C1)
INPUT7: IN7.2, U4.6 (C2)
INPUT8: IN8.2, U4.8 (C3)
IN_VCC: IN1.1, IN2.1, IN3.1, IN_V_SEL.2
unnamed: D1.A, R2.2
unnamed: R4.1, U1.3 (A1)
unnamed: R5.1, U1.5 (A2)
unnamed: R6.1, U1.7 (A3)
unnamed: R3.1, U1.1 (A)
unnamed: R7.1, U4.1 (A)
unnamed: R8.1, U4.3 (A1)
unnamed: R9.1, U4.5 (A2)
unnamed: R10.1, U4.7 (A3)
unnamed: LED3.A, R12.2
unnamed: LED2.A, R11.2
unnamed: LED4.A, R13.2
unnamed: R14.1, U5.2 (CATHODE)
unnamed: U3.6 (-INB), VR1.2 (WIPER)
unnamed: R15.2, VR1.1 (CCW)
unnamed: R16.1, VR1.3 (CW)
unnamed: C5.+, R17.1, U3.5 (+INB)
unnamed: U3.1 (OUTA), U3.2 (-INA)
unnamed: BT.1, R1.2
OUT1: OUT3.2, U6.10 (7C), U6.11 (6C), U6.12 (5C)
OUT2: OUT2.2, U6.13 (4C), U6.14 (3C)
OUT3: OUT1.2, U6.15 (2C), U6.16 (1C)
OUT_COM: OUT1.1, OUT2.1, OUT3.1, OUT_V_SEL.2, U6.9 (COM)
PWM_10V: C7.1, R21.2, RPM.2
RAW: D3.A, K1.1
RES: RESET.2, TB1.3 (RESET), TB1.28 (RESET)
RX: BT.2, TB1.2 (D0/RX)
SPEED: SPEED.2, TB1.26 (A7)
SPINDLE_ON-OFF: R11.1, TB1.7 (D4), U5.1 (ANODE), U6.1 (1B), U6.2 (2B)
SPINDLE_PWM: PWM.2, R22.2, TB1.8 (D5), U8.2 (A)
TX: R1.1, TB1.1 (D1/TX)
X_DIR: DIR2.2, TB1.19 (A0)
X_STEP: STEP.1, TB1.22 (A3)
Y_DIR: DIR2.1, TB1.20 (A1)
Y_STEP: STEP.2, TB1.23 (A4)
Z_DIR: DIR1.2, TB1.21 (A2)
Z_STEP: STEP.3, TB1.24 (A5)

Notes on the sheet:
PWM BUFFER WITH ITS OWN POWER SUPPLY
OUTPUT VOLTAGE SELECTOR
PWM TO 10V
INPUT VOLTAGE SELECTOR
OUTPUT INDICATORS
OUTPUT CONTROL
CON
5V POWER
BT HEADER
OMNIBUS ESTLCAM Edition
BY ALBERT KRAVCOV

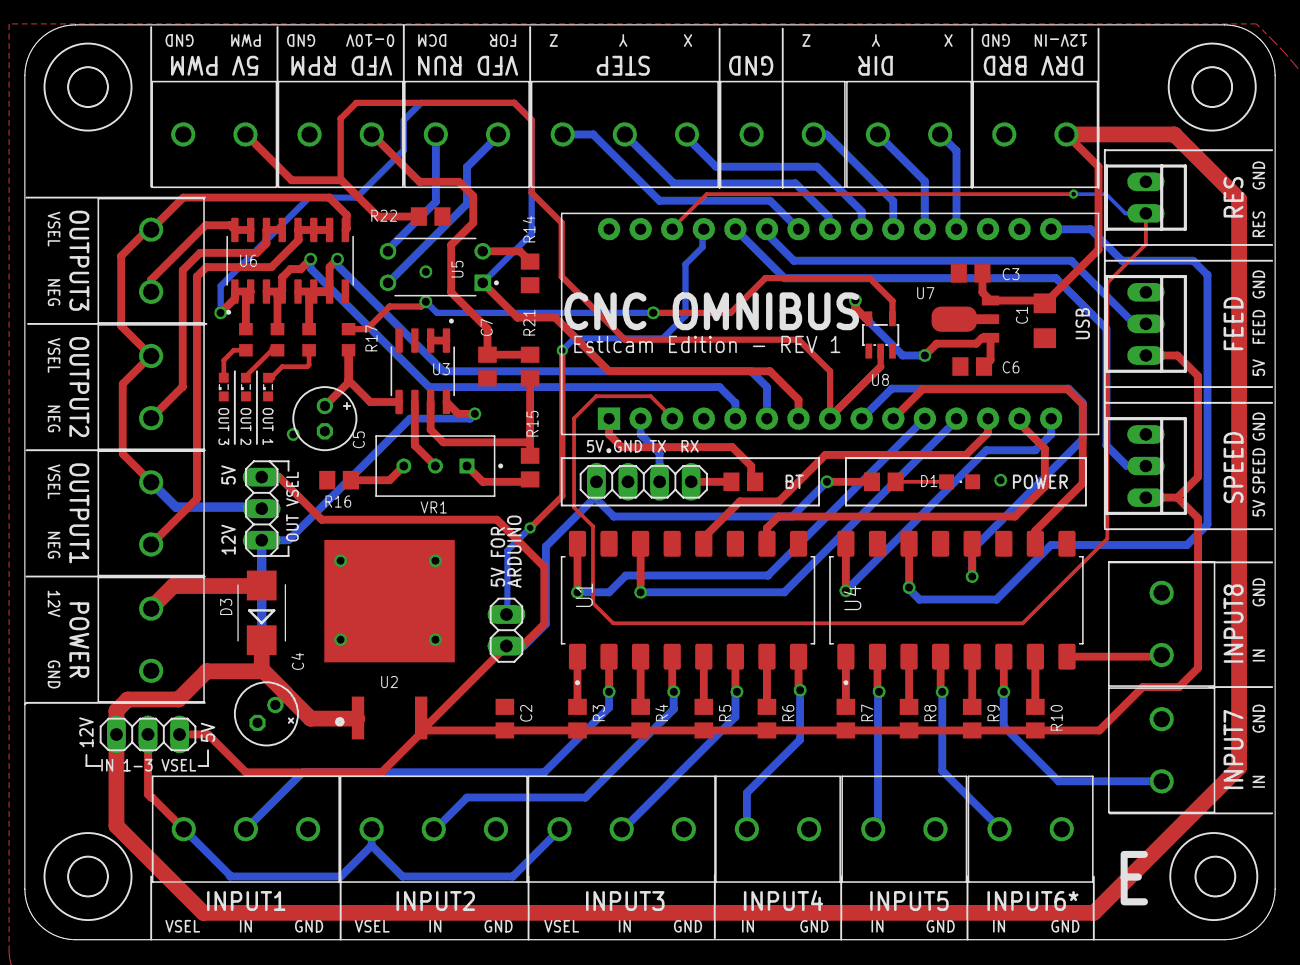
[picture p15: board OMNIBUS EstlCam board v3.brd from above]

Board: 2 copper layers, 100.6 x 73.6 mm, 67 parts (0 on the bottom side), 66 nets.

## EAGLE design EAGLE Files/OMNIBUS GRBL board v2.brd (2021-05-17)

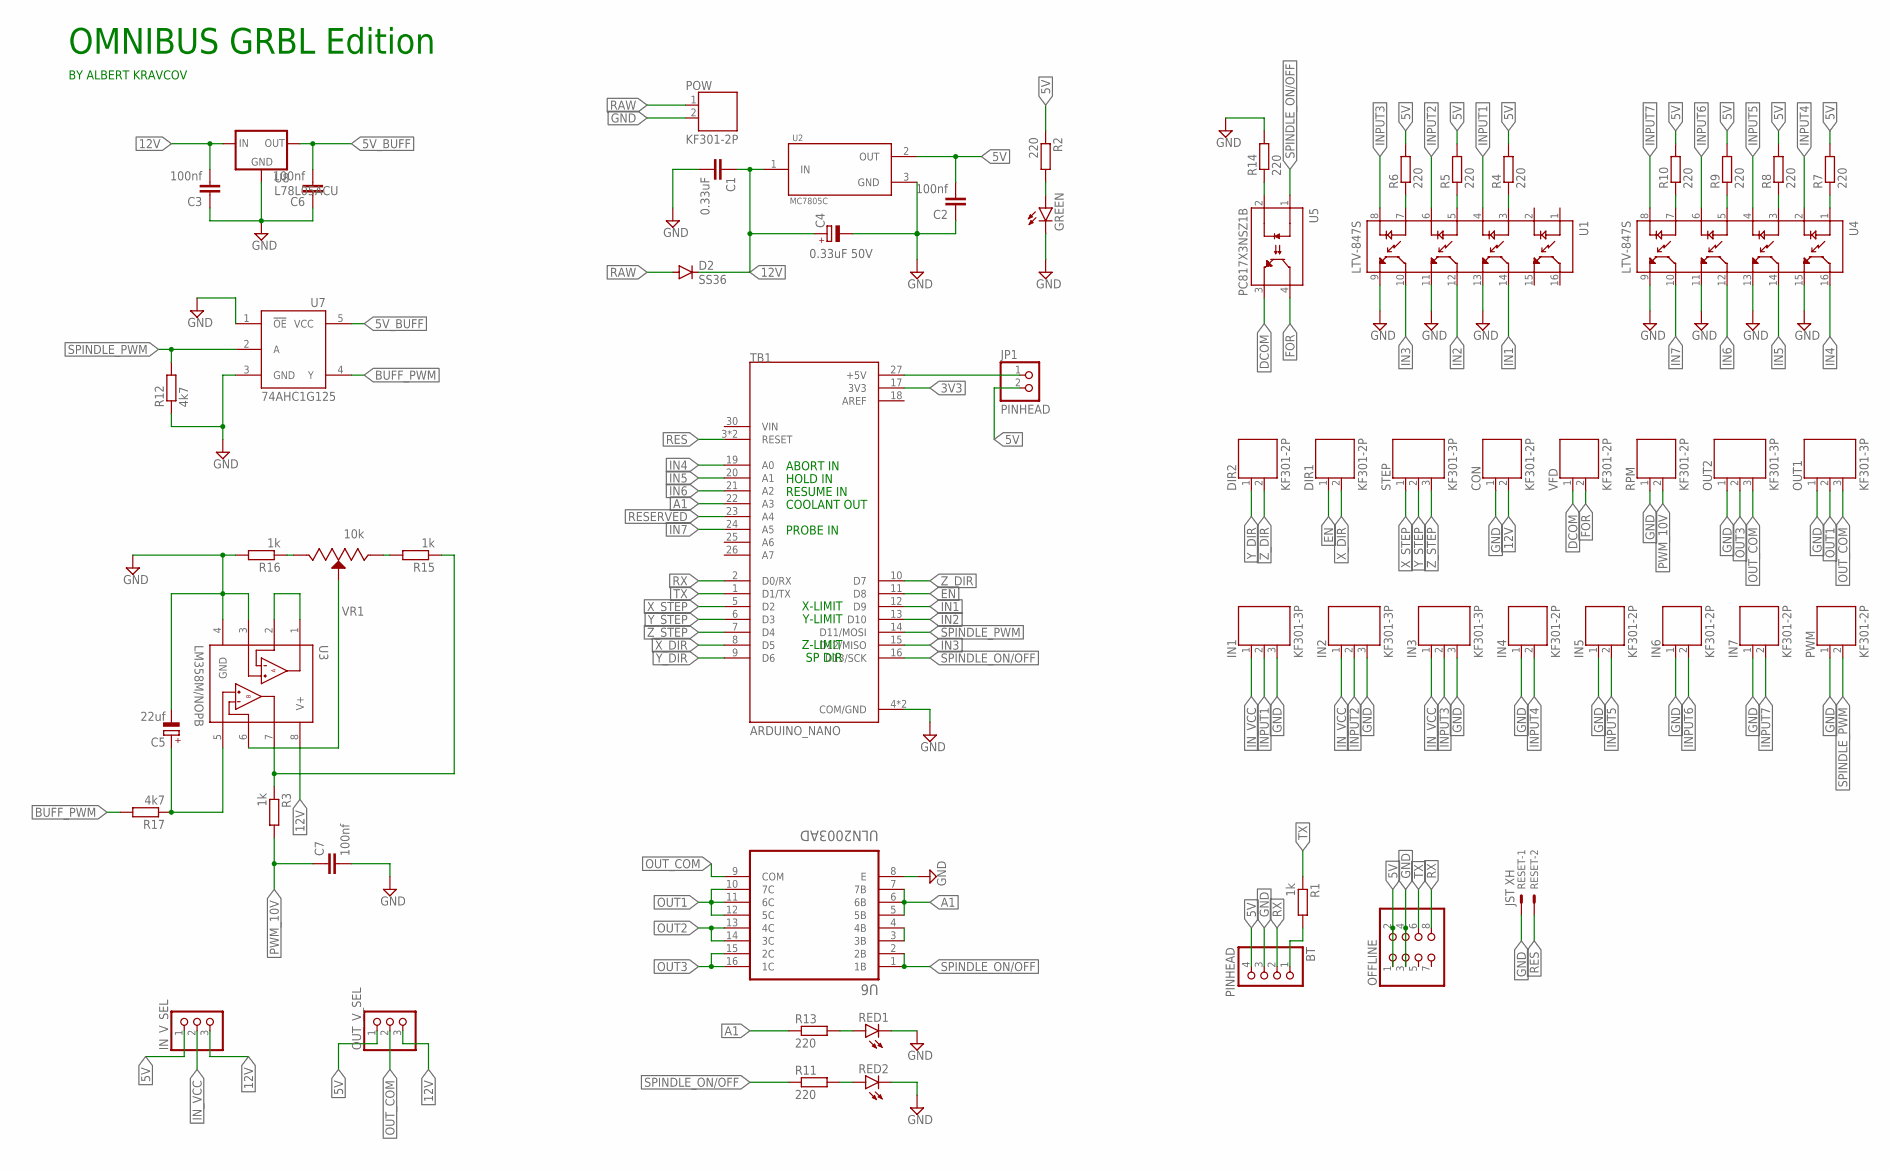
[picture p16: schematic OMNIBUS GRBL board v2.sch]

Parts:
BT: PINHEAD; 1X04
C1: 0.33uF; C1206K
C2: 100nf; C0805K
C3, C6, C7: 100nf; C0805
C4: 0.33uF 50V; E2-5
C5: 22uf; E2-5
CON: KF301-2P; 691131710002
D2: SS36; SMB
DIR1, DIR2: KF301-2P; 691131710002
GREEN: LEDCHIPLED_0805; CHIPLED_0805
IN1, IN2, IN3: KF301-3P; 691131710003
IN4, IN5, IN6, IN7: KF301-2P; 691131710002
IN_V_SEL: PINHD-1X3; 1X03
JP1: PINHEAD; 1X02
OFFLINE: PINHD-2X4; 2X04
OUT1, OUT2: KF301-3P; 691131710003
OUT_V_SEL: PINHD-1X3; 1X03
POW: KF301-2P; 691131710002
PWM: KF301-2P; 691131710002
R1, R3, R15, R16: 1k; R0805
R2, R11, R13: 220; R0603
R4, R5, R6, R7, R8, R9, R10, R14: 220; R0805
R12, R17: 4k7; R0805
RED1, RED2: LEDCHIPLED_0805; CHIPLED_0805
RESET: JST XH; 22-23-2021
RPM: KF301-2P; 691131710002
STEP: KF301-3P; 691131710003
TB1: ARDUINO_NANO; SHIELD_ARDUINO_NANO
U1, U4: LTV-847S; SOIC254P1016X460-16N
U2: MC7805C; TO254P1515X470-3N
U3: LM358M/NOPB; SOIC127P599X175-8N
U5: PC817X3NSZ1B; DIP762W50P254L495H455Q4
U6: ULN2003AD; SOIC127P600X175-16N
U7: 74AHC1G125; SOT23-5L
U8: L78L05ACU; SOT89
VFD: KF301-2P; 691131710002
VR1: 10k; TRIM_3296W-1-502

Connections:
3V3: TB1.17 (3V3)
5V: BT.4, C2.2, IN_V_SEL.1, JP1.2, OFFLINE.1, OFFLINE.2, OUT_V_SEL.1, R2.1, R4.2, R5.2, R6.2, R7.2, R8.2, R9.2, R10.2, U2.2 (OUT)
5V_BUFF: C6.2, U7.5 (VCC), U8.1 (OUT)
12V: C1.1, C3.2, C4.+, CON.2, D2.C, IN_V_SEL.3, OUT_V_SEL.3, U2.1 (IN), U3.8 (V+), U8.3 (IN)
A1: R13.1, TB1.22 (A3), U6.5 (5B), U6.6 (6B), U6.7 (7B)
A2: U6.3 (3B), U6.4 (4B)
ARDUPWR: JP1.1, TB1.27 (+5V)
AREF: TB1.18 (AREF)
BUFF_PWM: R17.2, U7.4 (Y)
DCOM: U5.3 (EMITTER), VFD.1
EN: DIR1.1, TB1.11 (D8)
FOR: U5.4 (COLLECTOR), VFD.2
GND: BT.3, C1.2, C2.1, C3.1, C4.-, C5.-, C6.1, C7.2, CON.1, GREEN.C, IN1.3, IN2.3, IN3.3, IN4.1, IN5.1, IN6.1, IN7.1, OFFLINE.3, OFFLINE.4, OUT1.1, OUT2.1, POW.2, PWM.1, R12.1, R14.2, R16.2, RED1.C, RED2.C, RESET.1, RPM.1, TB1.4 (COM/GND), TB1.29 (COM/GND), U1.9 (ET3), U1.11 (ET2), U1.13 (ET1), U2.3 (GND), U3.3 (+INA), U3.4 (GND), U4.9 (ET3), U4.11 (ET2), U4.13 (ET1), U4.15 (ET), U6.8 (E), U7.1 (!OE), U7.3 (GND), U8.2 (GND)
IN1: TB1.12 (D9), U1.14 (CT1)
IN2: TB1.13 (D10), U1.12 (CT2)
IN3: TB1.15 (D12/MISO), U1.10 (CT3)
IN4: TB1.19 (A0), U4.16 (CT)
IN5: TB1.20 (A1), U4.14 (CT1)
IN6: TB1.21 (A2), U4.12 (CT2)
IN7: TB1.24 (A5), U4.10 (CT3)
INPUT1: IN1.2, U1.4 (C1)
INPUT2: IN2.2, U1.6 (C2)
INPUT3: IN3.2, U1.8 (C3)
INPUT4: IN4.2, U4.2 (C)
INPUT5: IN5.2, U4.4 (C1)
INPUT6: IN6.2, U4.6 (C2)
INPUT7: IN7.2, U4.8 (C3)
IN_VCC: IN1.1, IN2.1, IN3.1, IN_V_SEL.2
unnamed: GREEN.A, R2.2
unnamed: R4.1, U1.3 (A1)
unnamed: R5.1, U1.5 (A2)
unnamed: R6.1, U1.7 (A3)
unnamed: R7.1, U4.1 (A)
unnamed: R8.1, U4.3 (A1)
unnamed: R9.1, U4.5 (A2)
unnamed: R10.1, U4.7 (A3)
unnamed: R11.2, RED2.A
unnamed: R13.2, RED1.A
unnamed: R14.1, U5.2 (CATHODE)
unnamed: U3.6 (-INB), VR1.2 (WIPER)
unnamed: R15.2, VR1.1 (CCW)
unnamed: R16.1, VR1.3 (CW)
unnamed: C5.+, R17.1, U3.5 (+INB)
unnamed: U3.1 (OUTA), U3.2 (-INA)
unnamed: BT.1, R1.2
OUT1: OUT1.2, U6.10 (7C), U6.11 (6C), U6.12 (5C)
OUT2: U6.13 (4C), U6.14 (3C)
OUT3: OUT2.2, U6.15 (2C), U6.16 (1C)
OUT_COM: OUT1.3, OUT2.3, OUT_V_SEL.2, U6.9 (COM)
PWM_10V: C7.1, R3.1, R3.2, R15.1, RPM.2, U3.7 (OUTB)
RAW: D2.A, POW.1
RES: RESET.2, TB1.3 (RESET), TB1.28 (RESET)
RESERVED: TB1.23 (A4)
RX: BT.2, OFFLINE.8, TB1.2 (D0/RX)
SPINDLE_ON/OFF: R11.1, TB1.16 (D13/SCK), U5.1 (ANODE), U6.1 (1B), U6.2 (2B)
SPINDLE_PWM: PWM.2, R12.2, TB1.14 (D11/MOSI), U7.2 (A)
TX: OFFLINE.6, R1.1, TB1.1 (D1/TX)
X_DIR: DIR1.2, TB1.8 (D5)
X_STEP: STEP.1, TB1.5 (D2)
Y_DIR: DIR2.1, TB1.9 (D6)
Y_STEP: STEP.2, TB1.6 (D3)
Z_DIR: DIR2.2, TB1.10 (D7)
Z_STEP: STEP.3, TB1.7 (D4)

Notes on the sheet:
SP DIR
ABORT IN
HOLD IN
RESUME IN
COOLANT OUT
PROBE IN
Z-LIMIT
Y-LIMIT
X-LIMIT
OMNIBUS GRBL Edition
BY ALBERT KRAVCOV

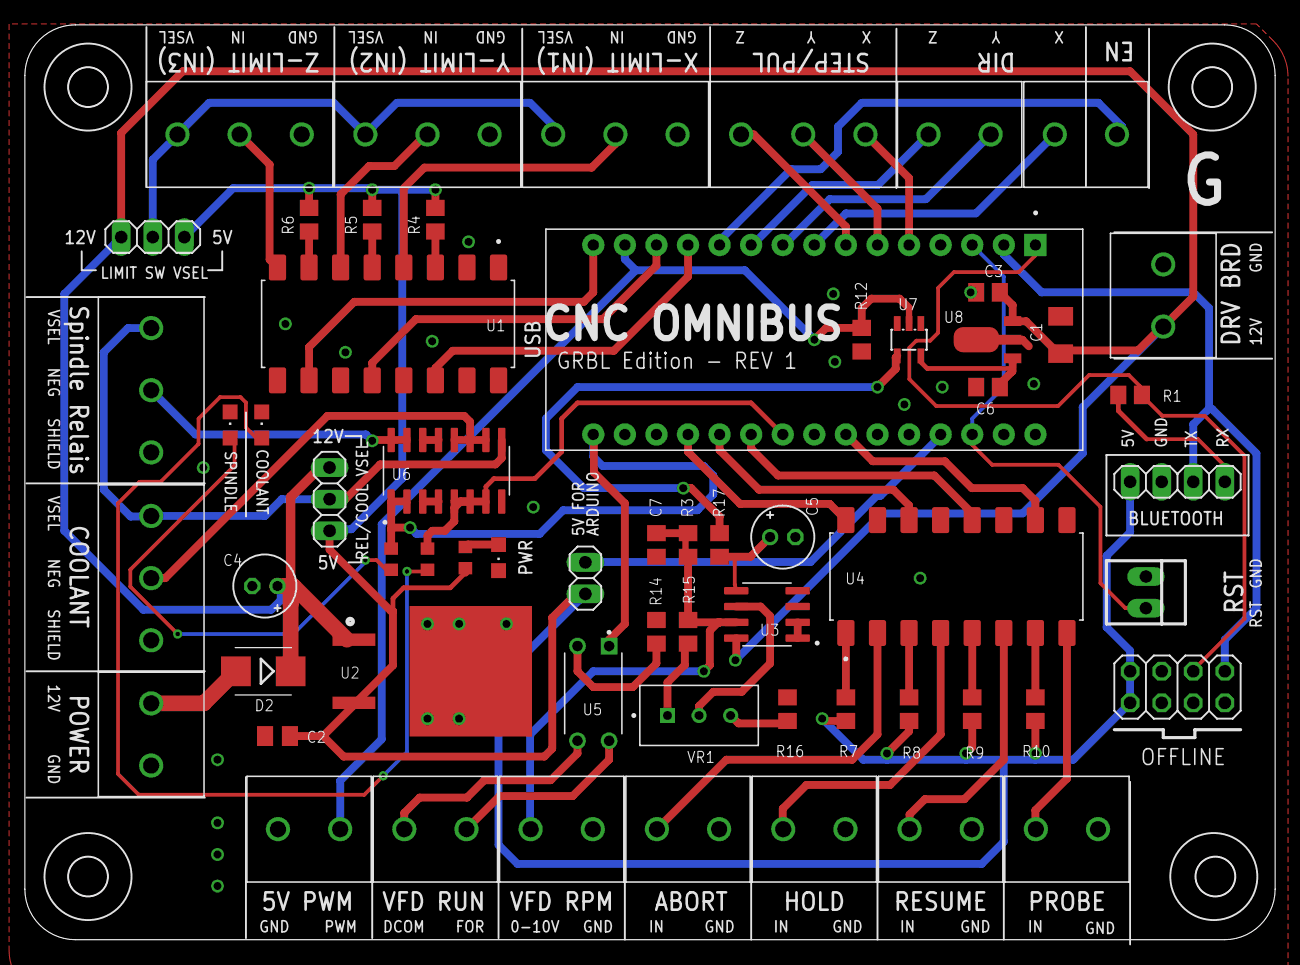
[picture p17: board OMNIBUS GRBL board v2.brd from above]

Board: 2 copper layers, 100.6 x 73.6 mm, 61 parts (0 on the bottom side), 60 nets.

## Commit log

2021-05-05 Initial File Upload
    [EstlCam board v3.brd, EstlCam board v3.sch, GRBL board v2.brd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]
2021-05-05 Renaming Files
    [OMNIBUS EstlCam board v3.brd, OMNIBUS EstlCam board v3.sch, OMNIBUS GRBL board v2.brd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]
2021-05-05 Extra files
    [40mm fan holder.dxf]
2021-05-05 STL Upload
    [Fan holder_fixed.stl]
2021-05-05 Update Fan holder.c4d
2021-05-05 label fix
    [OMNIBUS GRBL board v2.brd]
2021-05-06 PCB Bugfixes and polishing
    • DRV Shield had an routing error (laser indicator LED) also R3 had a wrong value
    • New Footprint for the 0.33uF Caps
    • Silkscreen polishing
    • almost all LEDs are 0805 package now
    [OMNIBUS EstlCam board v3.brd, OMNIBUS EstlCam board v3.sch, OMNIBUS GRBL board v2.brd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]
2021-05-07 Changed voltage regulators
    [OMNIBUS EstlCam board v3.brd, OMNIBUS EstlCam board v3.sch, OMNIBUS GRBL board v2.brd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]
2021-05-17 clean up
    also added BOM
    [OMNIBUS EstlCam board v3.brd, OMNIBUS EstlCam board v3.sch, OMNIBUS GRBL board v2.brd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]
2021-05-27 new DRV board version and updates
    [OMNIBUS Stepper board v3.brd, OMNIBUS Stepper board v3.sch]
2021-05-28 uninvert font
    [Fan holder.stl, Fan holder_fixed.stl]

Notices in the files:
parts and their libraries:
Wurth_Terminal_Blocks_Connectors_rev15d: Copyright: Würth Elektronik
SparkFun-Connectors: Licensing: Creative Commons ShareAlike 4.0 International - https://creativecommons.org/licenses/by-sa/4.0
